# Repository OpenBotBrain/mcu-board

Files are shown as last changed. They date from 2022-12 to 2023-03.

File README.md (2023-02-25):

# mcu-board

Some design notes for an MCU board...
Deeply WIP.

## Features

1. STM32 Cortex M4 with FSMC (possibility: STM32F413ZGT6 for 144-LQFP,
   STM32F413VGT3 for 100-LQFP, and STM32F413RGT6 for 64-LQFP)
2. Extra flash and PSRAM
2. WIFI module e.g. [ESP32 C3](https://www.espressif.com/sites/default/files/documentation/esp32-c3-mini-1_datasheet_en.pdf) or [ESP32 S3](https://www.espressif.com/sites/default/files/documentation/esp32-s3-mini-1_mini-1u_datasheet_en.pdf)
3. 4 motor control ports (EV3 compatible)
4. 4 sensor control ports (EV3 compatible)
5. Raspberry Pi pin-out connector (enough to communicate with
   Raspberry pi Zero, does not need full support)
5. SD card (SPI interface enough/SDIO nice to have but requires supported MCU)
6. Accelerometer (could be external)
7. STEMMA QT connector (nice to have)
8. Some informative display (nice to have)
9. A couple of buttons for interface (nice to have also)
10. Lego "compatible" physical shape.

### Alternative

- STM32L4R5VGT6 with 640KB of RAM instead of the external ram versions
  (but it also supports the FMC/FSMC). And it is cheap, and more
  available than the previous ones. (Or the subtly better STM32L4R5VIT6)

### Notes

- The [WIFI
  module](https://www.digikey.co.uk/en/products/detail/espressif-systems/ESP32-C3-MINI-1-H4/14548892)
  with the SD card on one side and the Raspberry Pi connector may not
  need to be active at the same time.
- The display could be controlled by the WIFI module via [AT
  commands](https://docs.espressif.com/projects/esp-at/en/latest/esp32/Compile_and_Develop/How_to_add_user-defined_AT_commands.html).
  Other things could be moved to the WIFI module too (the interface
  buttons, maybe).
- The board would be a [Raspberry Pi
  hat](https://github.com/raspberrypi/hats) that can work alone. This
  can be a rev 2 objective, but planning for the space would not hurt.
- Driving external memories with the FSMC, application not AN4761

# smaller mcu-board

## Features

1. STM32 Cortex M4 - May be
   - STM32L4P5CGT6
   - STM32L4P5CGT6P
   - STM32L4Q5CGT6
   - STM32L4Q5CGT6P
all (48-LQFP with 1MB of flash, and 320KB of RAM).

2. WIFI module e.g. [ESP32 C3](https://www.espressif.com/sites/default/files/documentation/esp32-c3-mini-1_datasheet_en.pdf) or [ESP32 S3](https://www.espressif.com/sites/default/files/documentation/esp32-s3-mini-1_mini-1u_datasheet_en.pdf)

3. 4 motor control ports (EV3 compatible)
4. 4 sensor control ports (EV3 compatible)

5. Raspberry Pi pin-out connector (enough to communicate with
   Raspberry pi Zero, does not need full support)

5. SD card (SPI interface enough/SDIO nice to have but requires supported MCU)
6. Accelerometer (could be external)
7. STEMMA QT connector (nice to have)
8. Some informative display and a couple of LEDs (nice to have)
9. A couple of buttons for interface (nice to have also)
10. Lego "compatible" physical shape.

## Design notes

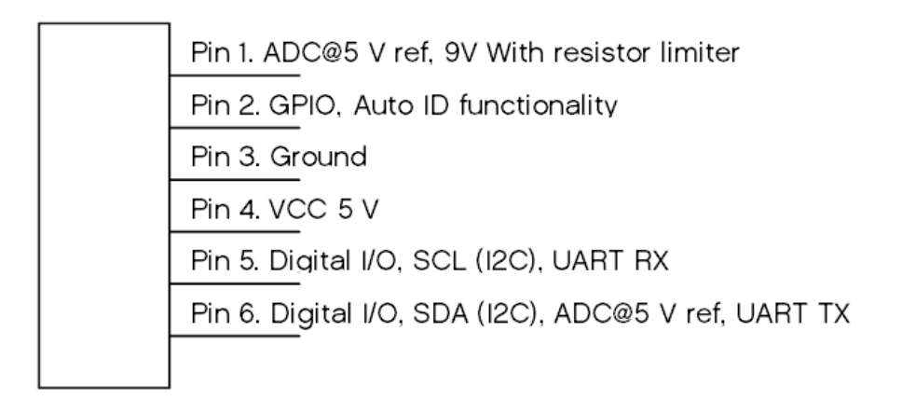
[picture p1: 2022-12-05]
PCB-RevA/input_port_pinout.png

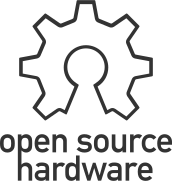
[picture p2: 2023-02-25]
PCB-RevA/OpenSourceHardware.png

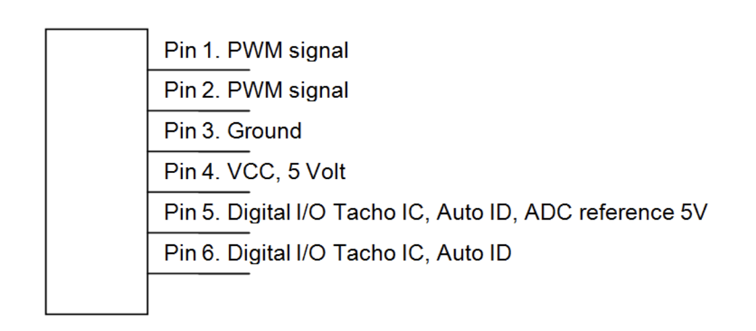
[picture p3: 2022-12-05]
PCB-RevA/ouput_port_pinout.png

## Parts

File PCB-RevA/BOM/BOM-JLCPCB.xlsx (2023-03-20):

Designator | Comment | Footprint | Qty | JLCPCB Part
C1, C4, C5, C6, C7, C8, C10, C12, C14, C18, C20, C23, C24, C25, C26, C27, C28, C29, C30, C31, C32, C38, C39, C41, C42, C45, C46, C52, C54, C55, C58, C62, C63, C68, C71, C72, C76, C93, C113, C141, C142, C143, C144, C145, C146, C166, C167, C168, C169, C170, C171, C180, C182 | 100n | Capacitor_SMD:C_0402_1005Metric | 53 | C1525 | https://www.lcsc.com/product-detail/Multilayer-Ceramic-Capacitors-MLCC-SMD-SMT_Samsung-Electro-Mechanics-CL05B104KO5NNNC_C1525.html
C2, C3, C16, C17, C19, C33, C34, C35, C36, C37, C43, C53, C90, C91, C92, C94, C99, C110, C110, C112, C114, C119, C132, C135, C140, C157, C160, C165, C181 | 1u 16V | Capacitor_SMD:C_0603_1608Metric | 29 | C59302 | https://www.lcsc.com/product-detail/Multilayer-Ceramic-Capacitors-MLCC-SMD-SMT_FH-Guangdong-Fenghua-Advanced-Tech-0603B105K250NT_C59302.html
C9, C49, C50, C51, C56, C73, C74, C75, C77, C78, C79 | 10u | Capacitor_SMD:C_0805_2012Metric | 11 | C1713 | https://www.lcsc.com/product-detail/Multilayer-Ceramic-Capacitors-MLCC-SMD-SMT_Samsung-Electro-Mechanics-CL21A106KOQNNNE_C1713.html
C11, C13, C60, C149, C174 | 4u7 16V | Capacitor_SMD:C_0603_1608Metric | 5 | C19666 | https://www.lcsc.com/product-detail/Multilayer-Ceramic-Capacitors-MLCC-SMD-SMT_Samsung-Electro-Mechanics-CL10A475KO8NNNC_C19666.html
C15, C80, C81, C86, C87, C88, C89, C97, C98, C108, C109, C117, C118, C128, C129, C133, C134, C138, C139, C150, C158, C159, C163, C164, C175 | 10n | Capacitor_SMD:C_0402_1005Metric | 25 | C15195 | https://www.lcsc.com/product-detail/Multilayer-Ceramic-Capacitors-MLCC-SMD-SMT_Samsung-Electro-Mechanics-CL05B103KB5NNNC_C15195.html
C21, C22 | 8p | Capacitor_SMD:C_0402_1005Metric | 2 | C610103 | https://www.lcsc.com/product-detail/Multilayer-Ceramic-Capacitors-MLCC-SMD-SMT_VIIYONG-V8R0D0402C0G500NBT_C610103.html
C40, C44, C57, C59, C61, C64, C65, C67, C70, C147, C172 | 10u 16V | Capacitor_SMD:C_0805_2012Metric | 11 | C1713 | https://www.lcsc.com/product-detail/Multilayer-Ceramic-Capacitors-MLCC-SMD-SMT_Samsung-Electro-Mechanics-CL21A106KOQNNNE_C1713.html
C47, C48, C95, C96, C100, C101, C102, C103, C104, C105, C106, C107, C115, C116, C120, C121, C122, C123, C124, C125, C126, C127, C130, C131, C136, C137, C151, C152, C153, C154, C155, C156, C161, C162, C176, C177, C178, C179 | 330p | Capacitor_SMD:C_0402_1005Metric | 38 | C13533 | https://www.lcsc.com/product-detail/Multilayer-Ceramic-Capacitors-MLCC-SMD-SMT_Samsung-Electro-Mechanics-CL05C331JB5NNNC_C13533.html
C66, C69, C148, C173 | 100uF 16V | Capacitor_SMD:CP_Elec_6.3x5.2 | 4 | C125975 | https://www.lcsc.com/product-detail/Aluminum-Electrolytic-Capacitors-SMD_Nichicon-UWT1V101MCL1GS_C125975.html
C82, C83 | 47p | Capacitor_SMD:C_0402_1005Metric | 2 | C1567 | https://www.lcsc.com/product-detail/Multilayer-Ceramic-Capacitors-MLCC-SMD-SMT_FH-Guangdong-Fenghua-Advanced-Tech-0402CG470J500NT_C1567.html
C84, C85 | 2.2n | Capacitor_SMD:C_0402_1005Metric | 2 | C1531 | https://www.lcsc.com/product-detail/Multilayer-Ceramic-Capacitors-MLCC-SMD-SMT_FH-Guangdong-Fenghua-Advanced-Tech-0402B222K500NT_C1531.html
D1, D2, D3, D3, D8, D9, D10 | LED | LED_SMD:LED_0402_1005Metric | 6 | C434447 | https://www.lcsc.com/product-detail/Light-Emitting-Diodes-LED_Yongyu-Photoelectric-SZYY0402B_C434447.html
D4, D5 | ESD5Zxx | Diode_SMD:D_SOD-523 | 2 | C5369351 | https://www.lcsc.com/product-detail/span-style-background-color-ff0-ESD-span-Protection-Devices_LGE-ESD5Z15_C5369351.html
D6, D7, D17, D18, D21, D22, D25, D26, D31, D32, D35, D36, D39, D40, D41, D42, D45, D46, D53, D54, D57, D58 | ESD9B5.0ST5G | Diode_SMD:D_SOD-923 | 22 | C2835422 | https://www.lcsc.com/product-detail/span-style-background-color-ff0-ESD-span-Protection-Devices_TECH-PUBLIC-ESD9B5VD_C2835422.html
D13, D14, D15, D16, D19, D20, D23, D24, D27, D28, D29, D30, D33, D34, D37, D38, D43, D44, D47, D48, D55, D56, D59, D60 | BAT54S | Package_TO_SOT_SMD:SOT-23 | 24 | C181201 | https://www.lcsc.com/product-detail/Schottky-Barrier-Diodes-SBD_Guangdong-Hottech-BAT54S_C181201.html
D49, D50, D51, D52, D61, D62, D63, D64 | SD12_SOD323 | Diode_SMD:D_SOD-323 | 8 | C521915 | https://www.lcsc.com/product-detail/ESD-Protection-Devices_TECH-PUBLIC-ESD5V0B03-323_C521915.html
F1, F2 | 8V 2A | Resistor_SMD:R_1812_4532Metric | 2 | C883156 | https://www.lcsc.com/product-detail/Resettable-Fuses_BHFUSE-BSMD1812-200-16V_C883156.html
F3, F4, F5, F6, F7, F8, F9, F10 | 30mA | Resistor_SMD:R_0603_1608Metric | 8 | C914090 | https://www.lcsc.com/product-detail/Resettable-Fuses_BHFUSE-BSMD0603-003-30V_C914090.html
J1 | DF11-10DP-2DSA | Connector_JST:JST_PHD_B10B-PHDSS_2x05_P2.00mm_Vertical | 1 | C597822 | https://www.lcsc.com/product-detail/Wire-To-Board-Wire-To-Wire-Connector_HRS-Hirose-DF11-10DP-2DSA-24_C597822.html
J3 | USB_C_Receptacle_USB2.0 | Connector_USB:USB_C_Receptacle_Palconn_UTC16-G | 1 | C2988369 | https://www.lcsc.com/product-detail/USB-Connectors_G-Switch-GT-USB-7010ASV_C2988369.html
L1 | 1.2uH 6.5A | Inductor_SMD:L_Chilisin_BMRA00050520 |  | C2041615 | https://www.lcsc.com/product-detail/Inductors-SMD_Vishay-Intertech-IHLP2020CZER1R5M11_C2041615.html
L2, L3 | 6.8uH 3.6A | Inductor_SMD:L_Ferrocore_DLG-0504 | 2 | C2847478 | https://www.lcsc.com/product-detail/Inductors-SMD_KOHERelec-MDA5030-6R8M_C2847478.html
Q1, Q2, Q3, Q5, Q6, Q9, Q10, Q11, Q12, Q17, Q18 | BSS84 | Package_TO_SOT_SMD:SOT-23 | 11 | C8492 | https://www.lcsc.com/product-detail/MOSFETs_LRC-LBSS84LT1G_C8492.html
Q4, Q7, Q8, Q13, Q15, Q16, Q19, Q20, Q27, Q28, Q29, Q30, Q31, Q32, Q33, Q34, Q35, Q36, Q37 | 2N7002 | Package_TO_SOT_SMD:SOT-23 | 19 | C8545 | https://www.lcsc.com/product-detail/MOSFETs_Jiangsu-Changjing-Electronics-Technology-Co-Ltd-2N7002_C8545.html
R1, R2, R3, R4, R6, R7, R8, R13, R14, R15, R16, R17, R18, R19, R20, R31, R33, R39, R40, R41, R43, R51, R53, R55, R57, R61, R62, R65, R68, R70, R71, R72, R73, R74, R75, R84, R85, R90, R91, R92, R93, R94, R95, R96, R97, R110, R111, R112, R114, R124, R125, R134, R135, R140, R141, R412, R143, R144, R145, R146, R147, R160, R161, R162, R164 | 10K | Resistor_SMD:R_0402_1005Metric | 65 | C25744 | https://www.lcsc.com/product-detail/Chip-Resistor-Surface-Mount_UNI-ROYAL-Uniroyal-Elec-0402WGF1002TCE_C25744.html
R5, R9, R28, R29, R30, R32, R34, R36, R37, R38, R44, R46, R48, R49, R52, R152 | 22 | Resistor_SMD:R_0402_1005Metric | 16 | C25092 | https://www.lcsc.com/product-detail/Chip-Resistor-Surface-Mount_UNI-ROYAL-Uniroyal-Elec-0402WGF220JTCE_C25092.html
R10, R11, R12, R23, R24, R25, R35, R50, R78, R79, R80, R81, R100, R101, R104, R105, R107, R109, R113, R115, R128, R129, R130, R131, R150, R151, R153, R163, R165, R184, R185, R198, R199, R202, R203, R204, R205, R206, R219, R220, R233, R234, R237, R238, R239, R240 | 330 | Resistor_SMD:R_0402_1005Metric | 46 | C25104 | https://www.lcsc.com/product-detail/Chip-Resistor-Surface-Mount_UNI-ROYAL-Uniroyal-Elec-0402WGF3300TCE_C25104.html
R21, R22, R26, R27, R45, R47, R54, R56, R69, R86, R87, R120, R121, R136, R137, R170, R171, R178, R179, R192, R193, R213, R214, R227, R228 | 2K4 | Resistor_SMD:R_0402_1005Metric | 25 | C25882 | https://www.lcsc.com/product-detail/Chip-Resistor-Surface-Mount_UNI-ROYAL-Uniroyal-Elec-0402WGF2401TCE_C25882.html
R42, R116, R118, R166, R168 | 220K | Resistor_SMD:R_0402_1005Metric | 5 | C25767 | https://www.lcsc.com/product-detail/Chip-Resistor-Surface-Mount_UNI-ROYAL-Uniroyal-Elec-0402WGF2203TCE_C25767.html
R58, R76, R77, R82, R83, R98, R99, R102, R103, R106, R108, R117, R119, R126, R127, R132, R133, R148, R149, R154, R167, R169, R174, R175, R180, R181, R186, R187, R188, R189, R194, R195, R200, R201, R209, R210, R215, R216, R221, R222, R223, R224, R229, R230, R235, R236 | 100K | Resistor_SMD:R_0402_1005Metric | 46 | C25741 | https://www.lcsc.com/product-detail/Chip-Resistor-Surface-Mount_UNI-ROYAL-Uniroyal-Elec-0402WGF1003TCE_C25741.html
R59, R67 | 29K4 | Resistor_SMD:R_0402_1005Metric | 2 | C327356 | https://www.lcsc.com/product-detail/Chip-Resistor-Surface-Mount_YAGEO-RC0402FR-0729K4L_C327356.html
R60, R63, R64, R66 | 51K | Resistor_SMD:R_0402_1005Metric | 4 | C25794 | https://www.lcsc.com/product-detail/Chip-Resistor-Surface-Mount_UNI-ROYAL-Uniroyal-Elec-0402WGF5102TCE_C25794.html
R88, R89, R122, R123, R138, R139, R172, R173, R176, R177, R182, R183, R190, R191, R196, R197, R211, R212, R217, R218, R225, R226, R231, R232 | 4K7 | Resistor_SMD:R_0402_1005Metric | 24 | C25900 | https://www.lcsc.com/product-detail/Chip-Resistor-Surface-Mount_UNI-ROYAL-Uniroyal-Elec-0402WGF4701TCE_C25900.html
R207, R208, R242, R243 | 0.43 | Resistor_SMD:R_0805_2012Metric | 4 | C3000778 | https://www.lcsc.com/product-detail/Chip-Resistor-Surface-Mount_FOJAN-FRL0805JR400TS_C3000778.html
SW1, SW2, SW3, SW5 | SW_Omron_B3FS | Button_Switch_SMD:SW_Push_1P1T_NO_6x6mm_H9.5mm | 4 | C255812 | https://www.lcsc.com/product-detail/Tactile-Switches_HYP-Hongyuan-Precision-1TS005F-2500-5001_C255812.html
U1 | LSM6DSL | Package_LGA:LGA-14_3x2.5mm_P0.5mm_LayoutBorder3x4y | 1 | C126672 | https://www.lcsc.com/product-detail/Attitude-Sensor-Gyroscope_STMicroelectronics-LSM6DSLTR_C126672.html
U2 | STM32L496ZGTx | Package_QFP:LQFP-144_20x20mm_P0.5mm | 1 | C1337220 | https://www.lcsc.com/product-detail/Microcontroller-Units-MCUs-MPUs-SOCs_STMicroelectronics-STM32L496ZGT6_C1337220.html
U4 | W25X40CLSS | Package_SO:SOIC-8_5.275x5.275mm_P1.27mm | 1 | C82317 (https://www.lcsc.com/product-detail/NOR-FLASH_Winbond-Elec-W25Q16JVSSIQ_C82317.html) | https://www.lcsc.com/product-detail/NOR-FLASH_Winbond-Elec-W25Q16JVSSIQ_C82317.html
U5 | FUSB302B01MPX | Package_DFN_QFN:WQFN-14-1EP_2.5x2.5mm_P0.5mm_EP1.45x1.45mm | 1 | C132291 | https://www.lcsc.com/product-detail/span-style-background-color-ff0-USB-span-ICs_onsemi-FUSB302BMPX_C132291.html
U6 | BQ25601 | Package_DFN_QFN:Texas_S-PWQFN-N24_EP2.7x2.7mm_ThermalVias | 1 | C468236 | https://www.lcsc.com/product-detail/Battery-Management-ICs_Texas-Instruments-BQ25601RTWR_C468236.html
U7 | AP2127K-3.3 | Package_TO_SOT_SMD:SOT-23-5 | 1 | C156285 | https://www.lcsc.com/product-detail/Linear-Voltage-Regulators-LDO_Diodes-Incorporated-AP2127K-3-3TRG1_C156285.html
U8, U9 | PAM2423AECADJR | Package_SO:SOIC-8-1EP_3.9x4.9mm_P1.27mm_EP2.29x3mm_ThermalVias | 2 | C781891 | https://www.lcsc.com/product-detail/DC-DC-Converters_Diodes-Incorporated-PAM2423AECADJR_C781891.html
U10, U11, U12, U18 | LMV324 | Package_SO:SOIC-14_3.9x8.7mm_P1.27mm | 4 | C362275 | https://www.lcsc.com/product-detail/Operational-Amplifier_Gainsil-LMV324-SR_C362275.html
U13, U14, U15, U16, U19, U20, U21, U22 | SN74LVC1G14DBV | Package_TO_SOT_SMD:SOT-23-5 | 8 | C434069 | https://www.lcsc.com/product-detail/Inverters_UMW-Youtai-Semiconductor-Co-Ltd-SN74LVC1G14DBVR_C434069.html
U17, U23 | DRV8833PWP | Package_SO:HTSSOP-16-1EP_4.4x5mm_P0.65mm_EP3.4x5mm_Mask2.46x2.31mm_ThermalVias | 2 | C50506 | https://www.lcsc.com/product-detail/Motor-Driver-ICs_Texas-Instruments-DRV8833PWPR_C50506.html
Y2 | 8Z-24.000MAAJ-T | Crystal:Crystal_SMD_Abracon_ABM10-4Pin_2.5x2.0mm | 1 | C284163 | https://www.lcsc.com/product-detail/Crystals_TAE-Zhejiang-Abel-Elec-TXM24M0004252BBCEO00T_C284163.html

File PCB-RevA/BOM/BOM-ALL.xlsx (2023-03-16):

Reference | Value | Footprint | Datasheet | Digi | Digikey | Field4 | Field5 | digi | Qty
C1, C4-C8, C10, C12, C14, C18, C20, C23-C32, C38, C39, C41, C42, C45, C46, C52, C54, C55, C58, C62, C63, C68, C71, C72, C76, C93, C113, C141-C146, C166-C171, C180, C182 | 100n | Capacitor_SMD:C_0402_1005Metric | https://www.digikey.co.uk/en/products/detail/samsung-electro-mechanics/CL05A104KA5NNNC/3886701 |  |  |  |  | https://www.digikey.co.uk/en/products/detail/samsung-electro-mechanics/CL05A104KA5NNNC/3886701 | 53 | https://www.lcsc.com/product-detail/Multilayer-Ceramic-Capacitors-MLCC-SMD-SMT_Samsung-Electro-Mechanics-CL05B104KO5NNNC_C1525.html
C2, C3, C16, C17, C19, C33-C37, C43, C53, C90-C92, C94, C99, C110-C112, C114, C119, C132, C135, C140, C157, C160, C165, C181 | 1u 16V | Capacitor_SMD:C_0603_1608Metric | https://www.digikey.co.uk/en/products/detail/samsung-electro-mechanics/CL10A105KA8NNNC/3886760 |  |  |  |  | https://www.digikey.co.uk/en/products/detail/samsung-electro-mechanics/CL10A105KA8NNNC/3886760 | 29 | https://www.lcsc.com/product-detail/Multilayer-Ceramic-Capacitors-MLCC-SMD-SMT_FH-Guangdong-Fenghua-Advanced-Tech-0603B105K250NT_C59302.html
C9, C49-C51, C56, C73-C75, C77-C79 | 10u | Capacitor_SMD:C_0805_2012Metric | https://www.digikey.co.uk/en/products/detail/samsung-electro-mechanics/CL21A106KOQNNNE/3886754 | https://www.digikey.co.uk/en/products/detail/samsung-electro-mechanics/CL21A106KOQNNNE/3886754 |  |  |  |  | 11 | https://www.lcsc.com/product-detail/Multilayer-Ceramic-Capacitors-MLCC-SMD-SMT_Samsung-Electro-Mechanics-CL21A106KOQNNNE_C1713.html
C11, C13, C60, C149, C174 | 4u7 16V | Capacitor_SMD:C_0603_1608Metric | https://www.digikey.co.uk/en/products/detail/samsung-electro-mechanics/CL10A105KA8NNNC/3886760 |  |  |  |  | https://www.digikey.co.uk/en/products/detail/samsung-electro-mechanics/CL10A105KA8NNNC/3886760 | 5 | https://www.lcsc.com/product-detail/Multilayer-Ceramic-Capacitors-MLCC-SMD-SMT_Samsung-Electro-Mechanics-CL10A475KO8NNNC_C19666.html
C15, C80, C81, C86-C89, C97, C98, C108, C109, C117, C118, C128, C129, C133, C134, C138, C139, C150, C158, C159, C163, C164, C175 | 10n | Capacitor_SMD:C_0402_1005Metric |  |  |  |  |  |  | 25 | https://www.lcsc.com/product-detail/Multilayer-Ceramic-Capacitors-MLCC-SMD-SMT_YAGEO-CC0402KRX7R9BB103_C60133.html
C21, C22 | 6p8 | Capacitor_SMD:C_0402_1005Metric |  |  |  |  |  |  | 2 | https://www.lcsc.com/product-detail/Multilayer-Ceramic-Capacitors-MLCC-SMD-SMT_FH-Guangdong-Fenghua-Advanced-Tech-0402CG6R8C500NT_C1576.html
C40, C44, C57, C59, C61, C64, C65, C67, C70, C147, C172 | 10u 16V | Capacitor_SMD:C_0805_2012Metric | https://www.digikey.co.uk/en/products/detail/samsung-electro-mechanics/CL21A106KOQNNNE/3886754 | https://www.digikey.co.uk/en/products/detail/samsung-electro-mechanics/CL21A106KOQNNNE/3886754 |  |  |  |  | 11 | https://www.lcsc.com/product-detail/Multilayer-Ceramic-Capacitors-MLCC-SMD-SMT_Samsung-Electro-Mechanics-CL21A106KOQNNNE_C1713.html
C47, C48, C95, C96, C100-C107, C115, C116, C120-C127, C130, C131, C136, C137, C151-C156, C161, C162, C176-C179 | 330p | Capacitor_SMD:C_0402_1005Metric |  |  |  |  |  |  | 38 | https://www.lcsc.com/product-detail/Multilayer-Ceramic-Capacitors-MLCC-SMD-SMT_YAGEO-CC0402KRX7R9BB331_C106206.html
C66, C69, C148, C173 | 100uF 16V | Capacitor_SMD:CP_Elec_6.3x5.2 | ~ |  |  |  |  |  | 4 | https://www.lcsc.com/product-detail/Aluminum-Electrolytic-Capacitors-SMD_Nichicon-UWT1V101MCL1GS_C125975.html
C82, C83 | 47p | Capacitor_SMD:C_0402_1005Metric |  |  |  |  |  |  | 2 | https://www.lcsc.com/product-detail/Multilayer-Ceramic-Capacitors-MLCC-SMD-SMT_YAGEO-CC0402JRNPO9BN470_C60137.html
C84, C85 | 2.2n | Capacitor_SMD:C_0402_1005Metric |  |  |  |  |  |  | 2 | https://www.lcsc.com/product-detail/Multilayer-Ceramic-Capacitors-MLCC-SMD-SMT_YAGEO-CC0402KRX7R9BB222_C106861.html
D1-D3, D8-D10 | LED | LED_SMD:LED_0402_1005Metric | ~ |  |  |  |  |  | 6 | https://www.lcsc.com/product-detail/Light-Emitting-Diodes-LED_Yongyu-Photoelectric-SZYY0402B_C434447.html
D4, D5 | ESD5Zxx | Diode_SMD:D_SOD-523 | https://www.onsemi.com/pdf/datasheet/esd5z2.5t1-d.pdf |  |  | https://www.digikey.co.uk/en/products/detail/littelfuse-inc/AQ3530-01LTG/11503998 |  |  | 2 | https://www.lcsc.com/product-detail/span-style-background-color-ff0-ESD-span-Protection-Devices_LGE-ESD5Z15_C5369351.html
D6, D7, D17, D18, D21, D22, D25, D26, D31, D32, D35, D36, D39-D42, D45, D46, D53, D54, D57, D58 | ESD9B5.0ST5G | Diode_SMD:D_SOD-923 | https://www.onsemi.com/pub/Collateral/ESD9B-D.PDF |  |  |  |  |  | 22 | https://www.lcsc.com/product-detail/span-style-background-color-ff0-ESD-span-Protection-Devices_TECH-PUBLIC-ESD9B5VD_C2835422.html
D11, D12 | FSV330AF | Diode_SMD:D_SOD-128 | ~ |  |  |  |  |  | 2 | https://www.lcsc.com/product-detail/Schottky-Barrier-Diodes-SBD_Comchip-ACDBC560-HF_C3019749.html
D13-D16, D19, D20, D23, D24, D27-D30, D33, D34, D37, D38, D43, D44, D47, D48, D55, D56, D59, D60 | BAT54S | Package_TO_SOT_SMD:SOT-23 | https://www.diodes.com/assets/Datasheets/ds11005.pdf |  |  |  |  |  | 24 | https://www.lcsc.com/product-detail/Schottky-Barrier-Diodes-SBD_Guangdong-Hottech-BAT54S_C181201.html
D49-D52, D61-D64 | SD12_SOD323 | Diode_SMD:D_SOD-323 | https://www.littelfuse.com/~/media/electronics/datasheets/tvs_diode_arrays/littelfuse_tvs_diode_array_sd_c_datasheet.pdf.pdf |  |  |  |  |  | 8
D65 | Inolux_IN-PI554FCH | LED_SMD:LED_Inolux_IN-PI554FCH_PLCC4_5.0x5.0mm_P3.2mm | http://www.inolux-corp.com/datasheet/SMDLED/Addressable%20LED/IN-PI554FCH.pdf |  |  |  |  |  | 1 | https://www.lcsc.com/product-detail/Light-Emitting-Diodes-LED_TCWIN-TX1813M5_C5137307.html
F1, F2 | 8V 2A | Resistor_SMD:R_1812_4532Metric | https://www.digikey.co.uk/en/products/detail/bel-fuse-inc/0ZCG0200FF2C/4156113 |  |  |  |  |  | 2 | https://www.lcsc.com/product-detail/Resettable-Fuses_BHFUSE-BSMD1812-200-16V_C883156.html
F3-F10 | 30mA | Resistor_SMD:R_0603_1608Metric | https://www.digikey.co.uk/en/products/detail/bel-fuse-inc/0ZCM0003FF2G/10270531 |  |  |  |  |  | 8 | https://www.lcsc.com/product-detail/Resettable-Fuses_BHFUSE-BSMD0603-003-30V_C914090.html
FID1-FID4 | Fiducial | Fiducial:Fiducial_1mm_Mask3mm | ~ |  |  |  |  |  | 4
H1-H4 | 3mm | MountingHole:MountingHole_3.2mm_M3_Pad | ~ |  |  |  |  |  | 4
J1 | DF11-10DP-2DSA | Connector_JST:JST_PHD_B10B-PHDSS_2x05_P2.00mm_Vertical | ~ |  |  |  |  |  | 1 | https://www.lcsc.com/product-detail/Wire-To-Board-Wire-To-Wire-Connector_HRS-Hirose-DF11-10DP-2DSA-24_C597822.html
J2 | Raspberry_Pi_2_3 | Connector_PinHeader_2.54mm:PinHeader_2x20_P2.54mm_Vertical | https://www.raspberrypi.org/documentation/hardware/raspberrypi/schematics/rpi_SCH_3bplus_1p0_reduced.pdf |  |  |  |  |  | 1
J3 | USB_C_Receptacle_USB2.0 | Connector_USB:USB_C_Receptacle_Palconn_UTC16-G | https://www.usb.org/sites/default/files/documents/usb_type-c.zip |  |  |  |  |  | 1 | https://www.lcsc.com/product-detail/USB-Connectors_G-Switch-GT-USB-7010ASV_C2988369.html
J4 | Conn_01x02 | Connector_JST:JST_PH_B2B-PH-K_1x02_P2.00mm_Vertical | https://www.digikey.co.uk/en/products/detail/jst-sales-america-inc/B02B-PASK-1-LF-SN/926738 |  |  |  |  |  | 1
J7-J14 | RJ12 | Connector_RJ:RJ12_Amphenol_54601 | https://www.digikey.co.uk/en/products/detail/assmann-wsw-components/A-2004-1-4-LP-N-R/2183634 |  |  |  |  |  | 8 | n/a
L1 | 1.2uH 6.5A | Inductor_SMD:L_Chilisin_BMRA00050520 | https://www.digikey.co.uk/en/products/detail/susumu/PCMB053T-1R2MS/3672031 |  |  |  |  |  | 1 | n/a
L2, L3 | 6.8uH 3.6A | Inductor_SMD:L_Ferrocore_DLG-0504 | https://www.digikey.co.uk/en/products/detail/tdk-corporation/VLS6045EX-6R8M/5287380 |  |  | VLS6045EX-6R8M |  |  | 2 | https://www.lcsc.com/product-detail/Inductors-SMD_KOHERelec-MDA5030-6R8M_C2847478.html
Q1-Q3, Q5, Q6, Q9-Q12, Q17, Q18 | BSS84 | Package_TO_SOT_SMD:SOT-23 | http://assets.nexperia.com/documents/data-sheet/BSS84.pdf |  |  |  |  |  | 11 | https://www.lcsc.com/product-detail/MOSFETs_FOSAN-BSS84_C2926187.html
Q4, Q7, Q8, Q13, Q15, Q16, Q19, Q20, Q27-Q37 | 2N7002 | Package_TO_SOT_SMD:SOT-23 | https://www.onsemi.com/pub/Collateral/NDS7002A-D.PDF |  |  |  |  |  | 19 | https://www.lcsc.com/product-detail/MOSFETs_JSMSEMI-2N7002_C916396.html
R1-R4, R6-R8, R13-R20, R31, R33, R39-R41, R43, R51, R53, R55, R57, R61, R62, R65, R68, R70-R75, R84, R85, R90-R97, R110-R112, R114, R124, R125, R134, R135, R140-R147, R160-R162, R164 | 10K | Resistor_SMD:R_0402_1005Metric | ~ |  |  |  |  |  | 65 | https://www.lcsc.com/product-detail/Chip-Resistor-Surface-Mount_YAGEO-RC0402FR-0710KL_C60490.html
R5, R9, R28-R30, R32, R34, R36-R38, R44, R46, R48, R49, R52, R152 | 22 | Resistor_SMD:R_0402_1005Metric | ~ |  |  |  |  |  | 16 | https://www.lcsc.com/product-detail/Chip-Resistor-Surface-Mount_UNI-ROYAL-Uniroyal-Elec-0402WGJ0220TCE_C25152.html
R10-R12, R23-R25, R35, R50, R78-R81, R100, R101, R104, R105, R107, R109, R113, R115, R128-R131, R150, R151, R153, R163, R165, R184, R185, R198, R199, R202-R206, R219, R220, R233, R234, R237-R240 | 330 | Resistor_SMD:R_0402_1005Metric | ~ |  |  |  |  |  | 46 | https://www.lcsc.com/product-detail/Chip-Resistor-Surface-Mount_UNI-ROYAL-Uniroyal-Elec-0402WGJ0331TCE_C12246.html
R21, R22, R26, R27, R45, R47, R54, R56, R69, R86, R87, R120, R121, R136, R137, R170, R171, R178, R179, R192, R193, R213, R214, R227, R228 | 2K4 | Resistor_SMD:R_0402_1005Metric | ~ |  |  |  |  |  | 25 | https://www.lcsc.com/product-detail/Chip-Resistor-Surface-Mount_YAGEO-RC0402FR-072K4L_C112296.html
R42, R116, R118, R166, R168 | 220K | Resistor_SMD:R_0402_1005Metric | ~ |  |  |  |  |  | 5 | https://www.lcsc.com/product-detail/Chip-Resistor-Surface-Mount_UNI-ROYAL-Uniroyal-Elec-0402WGF2203TCE_C25767.html
R58, R76, R77, R82, R83, R98, R99, R102, R103, R106, R108, R117, R119, R126, R127, R132, R133, R148, R149, R154, R167, R169, R174, R175, R180, R181, R186-R189, R194, R195, R200, R201, R209, R210, R215, R216, R221-R224, R229, R230, R235, R236 | 100K | Resistor_SMD:R_0402_1005Metric | ~ |  |  |  |  |  | 46 | https://www.lcsc.com/product-detail/Chip-Resistor-Surface-Mount_YAGEO-RC0402FR-07100KL_C60491.html
R59, R67 | 29K4 | Resistor_SMD:R_0402_1005Metric | ~ | https://www.digikey.co.uk/en/products/detail/stackpole-electronics-inc/RMCF0402FT29K4/1761483 |  |  |  |  | 2 | https://www.lcsc.com/product-detail/Chip-Resistor-Surface-Mount_YAGEO-RC0402FR-0729K4L_C327356.html
R60, R63, R64, R66 | 51K | Resistor_SMD:R_0402_1005Metric | ~ | https://www.digikey.co.uk/en/products/detail/stackpole-electronics-inc/RMCF0402FT29K4/1761483 |  |  |  |  | 4 | https://www.lcsc.com/product-detail/Chip-Resistor-Surface-Mount_UNI-ROYAL-Uniroyal-Elec-0402WGF5102TCE_C25794.html
R88, R89, R122, R123, R138, R139, R172, R173, R176, R177, R182, R183, R190, R191, R196, R197, R211, R212, R217, R218, R225, R226, R231, R232 | 4K7 | Resistor_SMD:R_0402_1005Metric | ~ |  |  |  |  |  | 24 | https://www.lcsc.com/product-detail/Chip-Resistor-Surface-Mount_YAGEO-RC0402FR-074K7L_C105871.html
R207, R208, R242, R243 | 0.43 | Resistor_SMD:R_0805_2012Metric | https://www.digikey.co.uk/en/products/detail/panasonic-electronic-components/ERJ-6DQFR43V/6004382 |  |  |  |  |  | 4 | https://www.lcsc.com/product-detail/Chip-Resistor-Surface-Mount_FOJAN-FRL0805JR430TS_C2930326.html
SW1-SW3, SW5 | SW_Omron_B3FS | Button_Switch_SMD:SW_Push_1P1T_NO_6x6mm_H9.5mm | https://omronfs.omron.com/en_US/ecb/products/pdf/en-b3fs.pdf |  |  |  |  |  | 4 | n/a?
SYMBOL1 |  | CustomLibrary:sggtav_logo |  |  |  |  |  |  | 1
SYMBOL2 |  | CustomLibrary:lego_robot_controller |  |  |  |  |  |  | 1
SYMBOL3 |  | CustomLibrary:open_source |  |  |  |  |  |  | 1
TP1-TP14, TP16, TP18, TP20, TP22, TP24-TP27, TP29-TP101, TP103-TP120, TP122-TP132, TP134-TP145, TP148 | S1mm | TestPoint:TestPoint_Pad_1.0x1.0mm | ~ |  |  |  |  |  | 137
TP15, TP17, TP19, TP21, TP23, TP28, TP133, TP146, TP147, TP149 | TH1mm | TestPoint:TestPoint_THTPad_1.0x1.0mm_Drill0.5mm | ~ |  |  |  |  |  | 10
U1 | LSM6DSL | Package_LGA:LGA-14_3x2.5mm_P0.5mm_LayoutBorder3x4y | https://www.st.com/resource/en/datasheet/lsm6dsl.pdf |  |  |  |  |  | 1 | https://www.lcsc.com/product-detail/Attitude-Sensor-Gyroscope_STMicroelectronics-LSM6DSLTR_C126672.html
U2 | STM32L496ZGTx | Package_QFP:LQFP-144_20x20mm_P0.5mm | https://www.st.com/resource/en/datasheet/stm32l496zg.pdf |  |  |  |  |  | 1 | https://www.lcsc.com/product-detail/Microcontroller-Units-MCUs-MPUs-SOCs_STMicroelectronics-STM32L496ZGT6_C1337220.html
U3 | SSD1306 | SSD1306:128x64OLED |  |  |  |  |  |  | 1
U4 | W25X40CLSS | Package_SO:SOIC-8_5.275x5.275mm_P1.27mm | https://www.winbond.com/resource-files/W25X40CL_G%2020210505.pdf |  |  |  |  |  | 1 | https://www.lcsc.com/product-detail/NOR-FLASH_Winbond-Elec-W25Q16JVSNIQ_C115407.html
U5 | FUSB302B01MPX | Package_DFN_QFN:WQFN-14-1EP_2.5x2.5mm_P0.5mm_EP1.45x1.45mm | http://www.onsemi.com/pub/Collateral/FUSB302B-D.PDF |  |  |  |  |  | 1 | https://www.lcsc.com/product-detail/span-style-background-color-ff0-USB-span-ICs_onsemi-FUSB302BMPX_C132291.html
U6 | BQ25601 | Package_DFN_QFN:Texas_S-PWQFN-N24_EP2.7x2.7mm_ThermalVias | http://www.ti.com/lit/ds/symlink/bq25601.pdf |  |  |  |  |  | 1 | https://www.lcsc.com/product-detail/Battery-Management-ICs_Texas-Instruments-BQ25601RTWR_C468236.html
U7 | AP2127K-3.3 | Package_TO_SOT_SMD:SOT-23-5 | https://www.diodes.com/assets/Datasheets/AP2127.pdf |  |  |  |  |  | 1 | https://www.lcsc.com/product-detail/Linear-Voltage-Regulators-LDO_Diodes-Incorporated-AP2127K-3-3TRG1_C156285.html
U8, U9 | PAM2423AECADJR | Package_SO:SOIC-8-1EP_3.9x4.9mm_P1.27mm_EP2.29x3mm_ThermalVias | https://www.diodes.com/assets/Datasheets/products_inactive_data/PAM2421_22_23.pdf |  | https://www.digikey.co.uk/en/products/detail/diodes-incorporated/PAM2423AECADJR/4033258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 |  |  |  | 2 | https://www.lcsc.com/product-detail/DC-DC-Converters_Diodes-Incorporated-PAM2423AECADJR_C781891.html
U10-U12, U18 | LMV324 | Package_SO:SOIC-14_3.9x8.7mm_P1.27mm | http://www.ti.com/lit/ds/symlink/lmv324.pdf |  |  |  |  |  | 4 | https://www.lcsc.com/product-detail/Operational-Amplifier_TECH-PUBLIC-LMV324_C5342379.html
U13-U16, U19-U22 | SN74LVC1G14DBV | Package_TO_SOT_SMD:SOT-23-5 | http://www.ti.com/lit/ds/symlink/sn74lvc1g14.pdf |  |  |  |  |  | 8 | https://www.lcsc.com/product-detail/Gates_UMW-Youtai-Semiconductor-Co-Ltd-SN74LVC1G14DCKR_C2976657.html
U17, U23 | DRV8833PWP | Package_SO:HTSSOP-16-1EP_4.4x5mm_P0.65mm_EP3.4x5mm_Mask2.46x2.31mm_ThermalVias | http://www.ti.com/lit/ds/symlink/drv8833.pdf |  |  |  |  |  | 2 | https://www.lcsc.com/product-detail/Motor-Driver-ICs_Texas-Instruments-DRV8833PWPR_C50506.html
Y2 | 8Z-24.000MAAJ-T | Crystal:Crystal_SMD_Abracon_ABM10-4Pin_2.5x2.0mm | ~ |  |  |  |  |  | 1 | https://datasheet.lcsc.com/lcsc/1810171034_TAE-Zhejiang-Abel-Elec-TXM24M0004252BBCEO00T_C284163.pdf

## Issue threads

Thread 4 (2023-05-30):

Add a SW to turn on 5V reg and 9V power supply

sggtav, 2023-05-30:
This is to avoid high current spikes when capacitors are getting charged.

sggtav, 2023-10-28:
For testing, we connected a P most in the 4.2 input rail, and the gate is controlled by the uC. This works perfecly

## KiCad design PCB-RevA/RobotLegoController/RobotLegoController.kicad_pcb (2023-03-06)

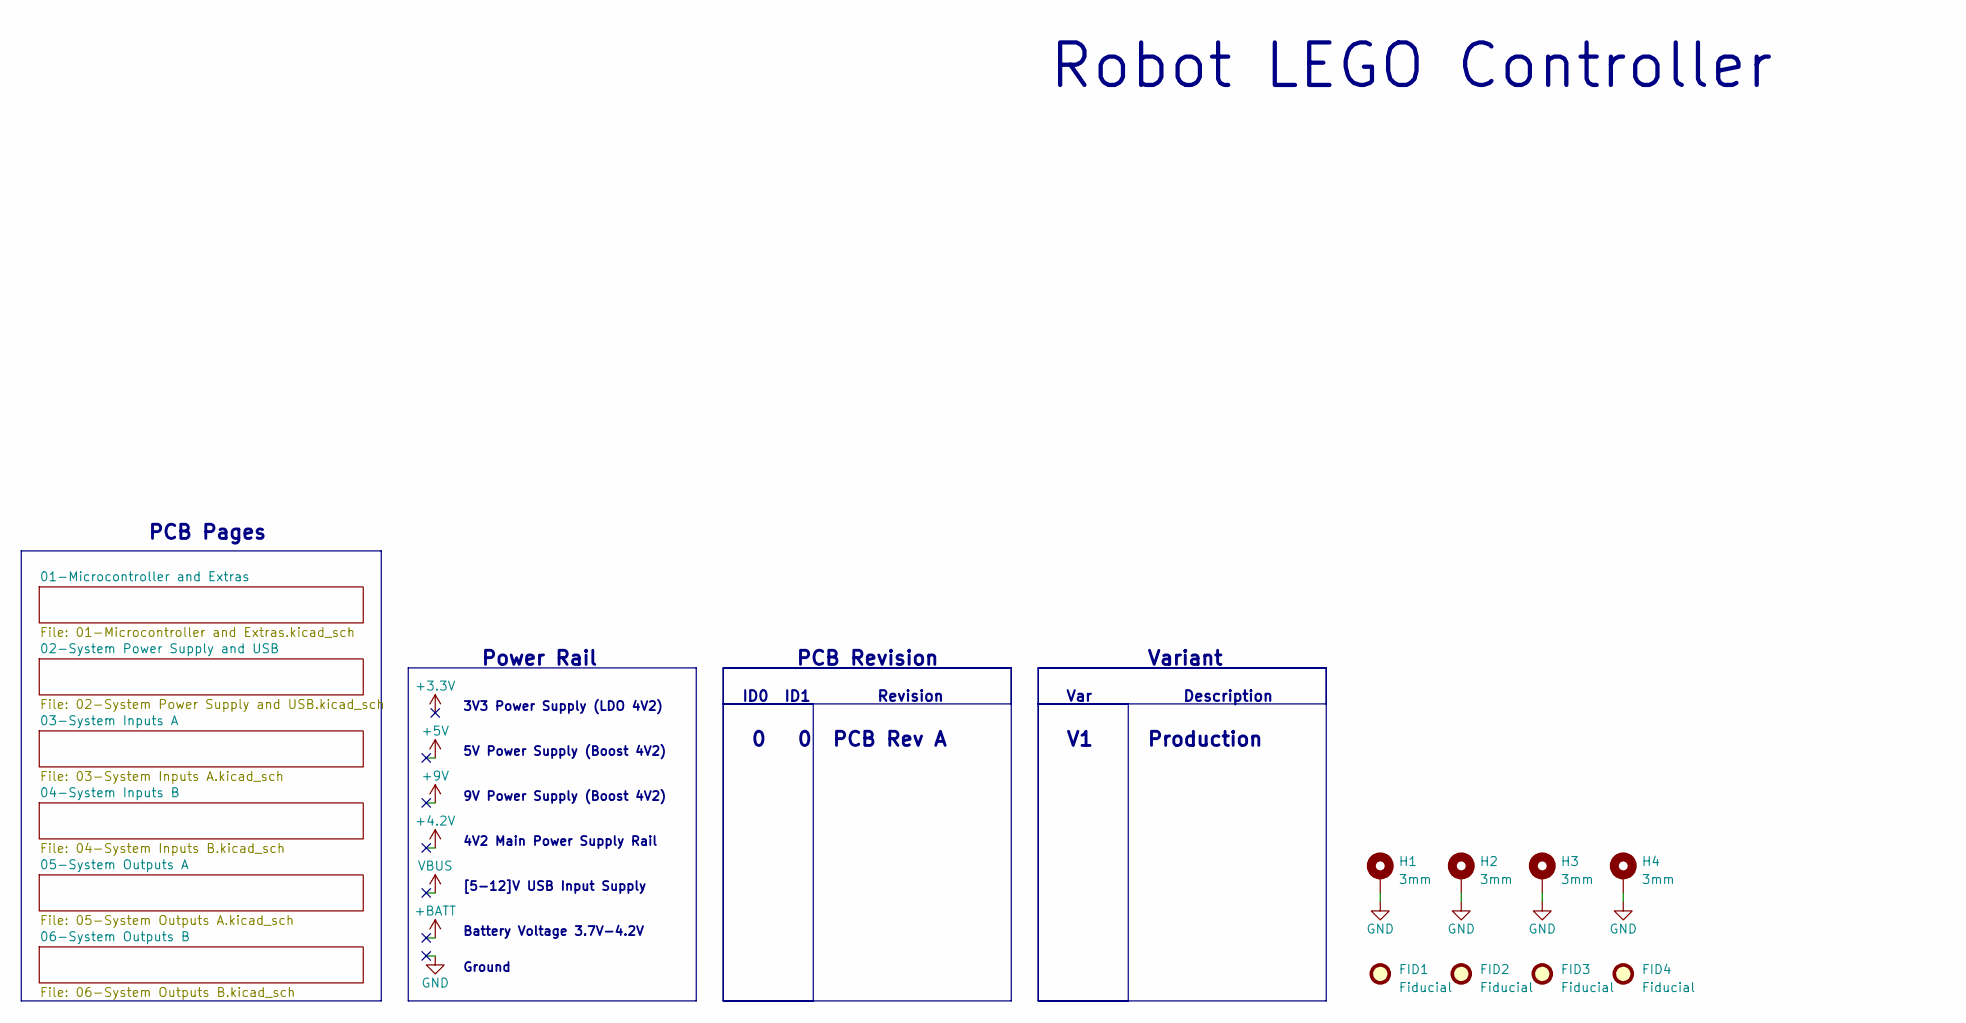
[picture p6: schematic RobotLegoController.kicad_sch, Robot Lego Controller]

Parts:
FID1, FID2, FID3, FID4: Fiducial; Fiducial_1mm_Mask3mm
H1, H2, H3, H4: 3mm; MountingHole_3.2mm_M3_Pad

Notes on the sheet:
Power Rail
Var
0 0
ID0 ID1
9V Power Supply (Boost 4V2)
3V3 Power Supply (LDO 4V2)
Battery Voltage 3.7V-4.2V
Variant
[5-12]V USB Input Supply
Description
Production
PCB Revision
PCB Rev A
4V2 Main Power Supply Rail
Revision
PCB Pages
Ground
5V Power Supply (Boost 4V2)
Robot LEGO Controller

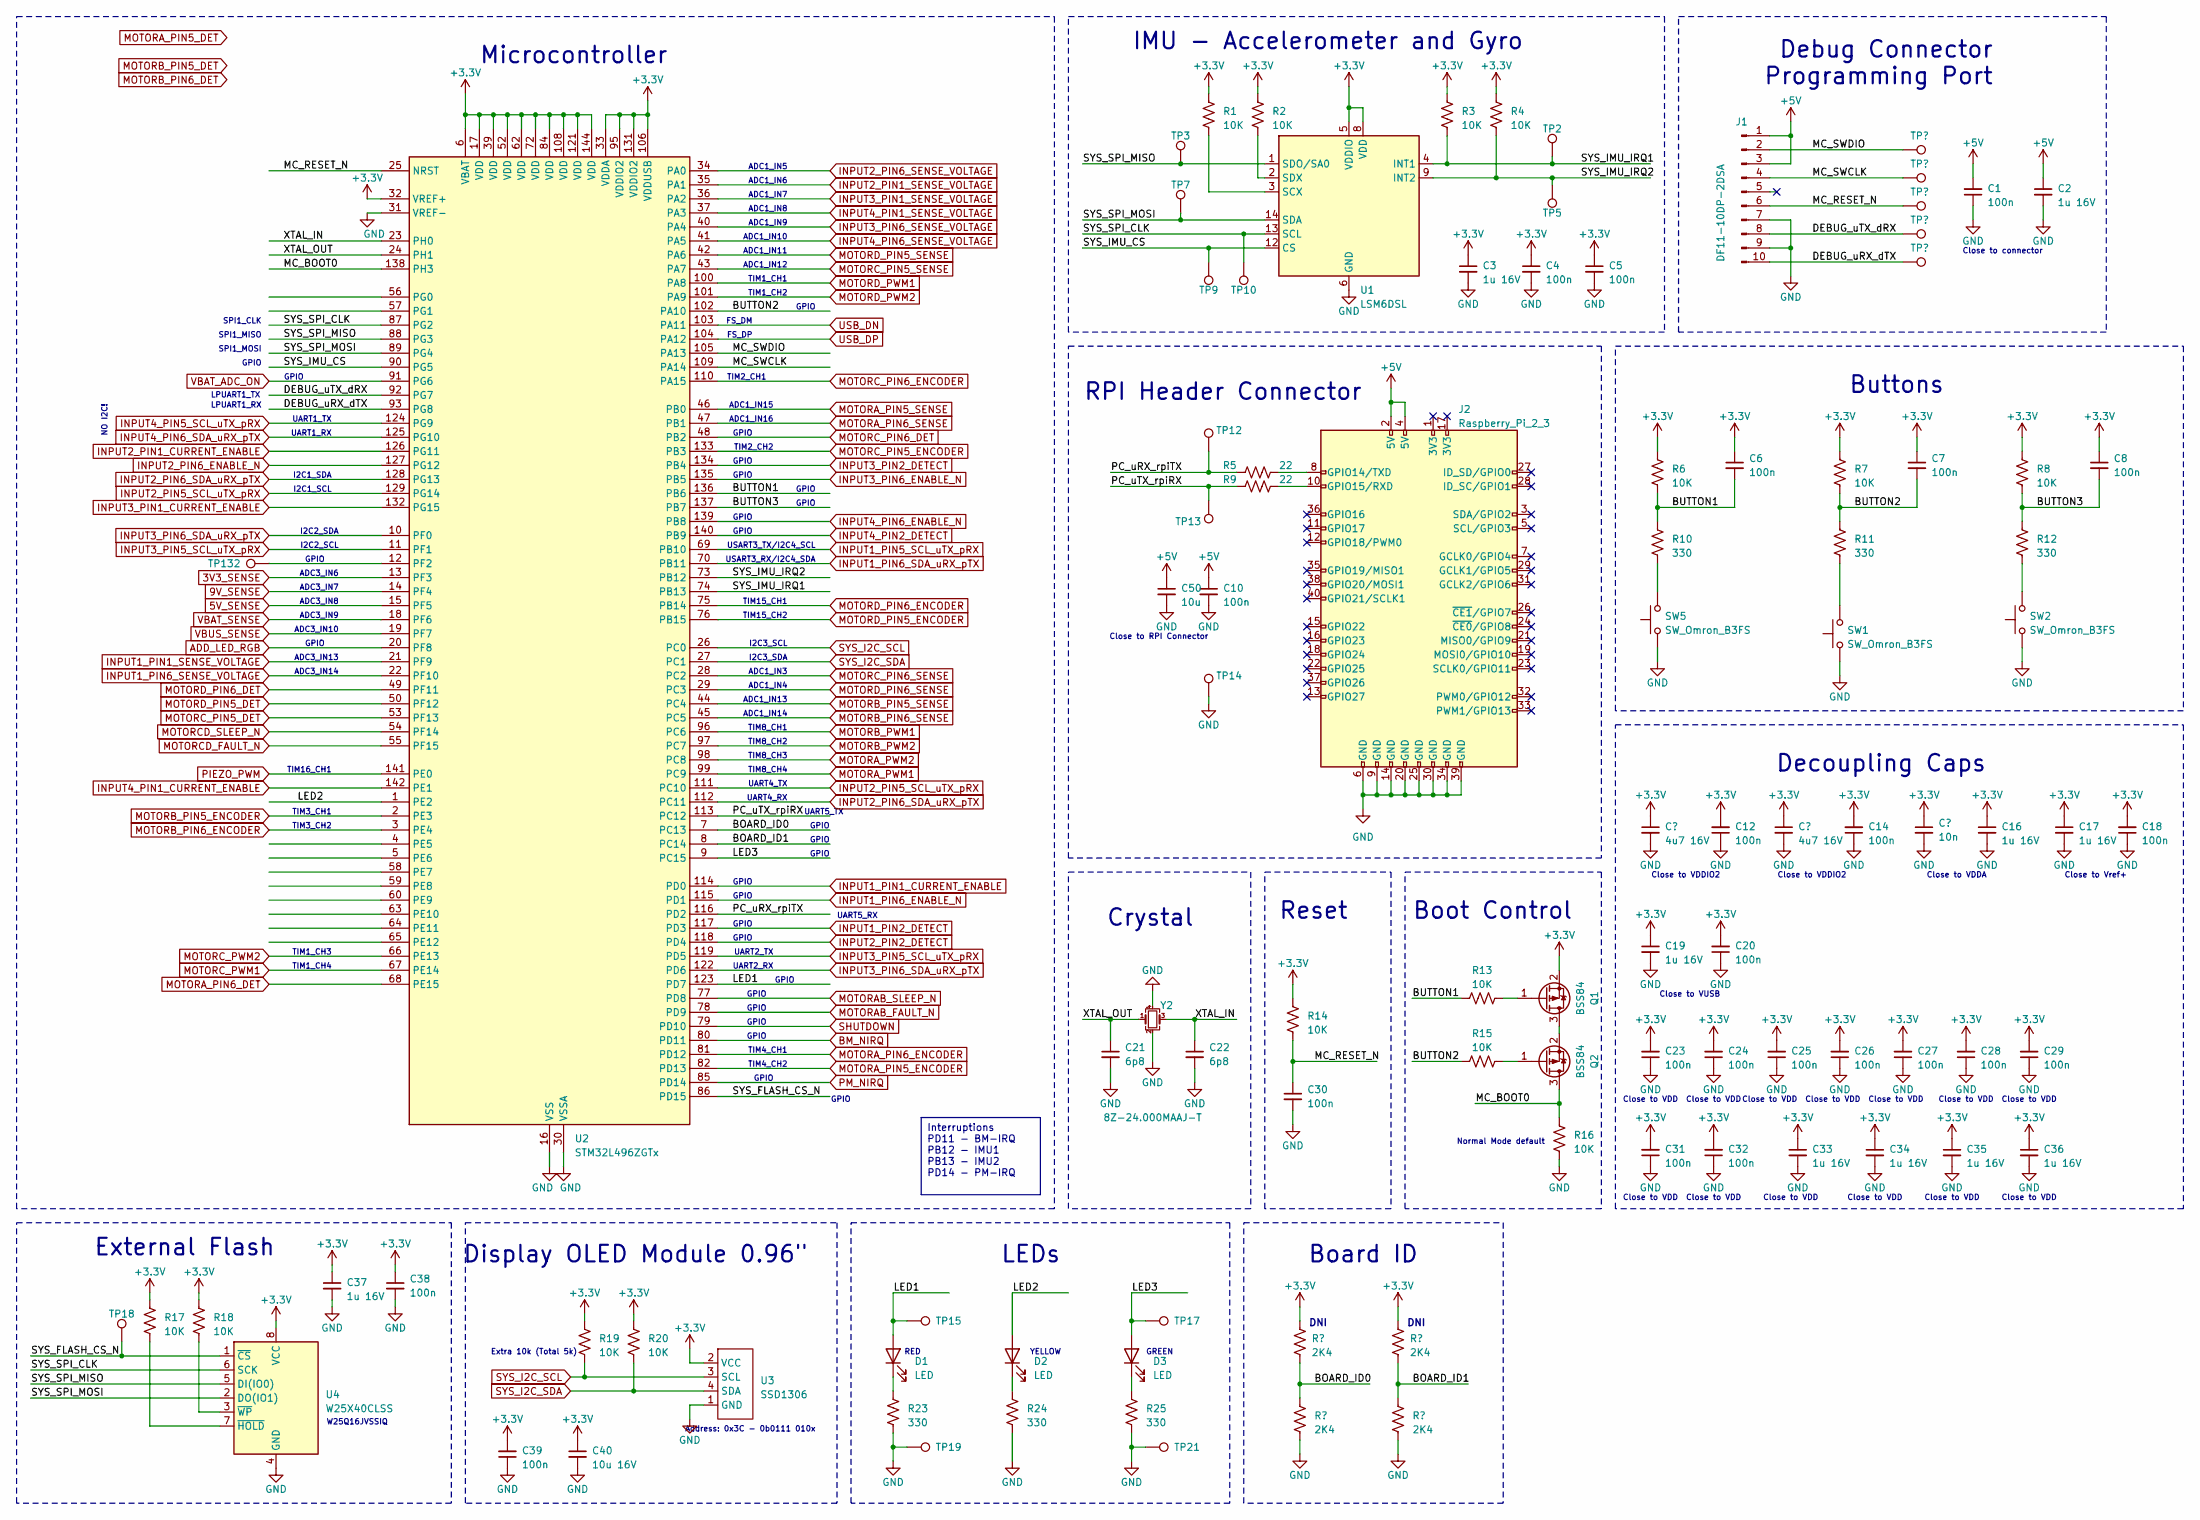
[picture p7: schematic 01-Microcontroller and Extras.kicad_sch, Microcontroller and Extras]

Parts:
C1, C4, C5, C6, C7, C8, C10, C12, C14, C18, C20, C23, C24, C25, C26, C27, C28, C29, C30, C31, C32, C38, C39: 100n; C_0402_1005Metric
C2, C3, C16, C17, C19, C33, C34, C35, C36, C37: 1u 16V; C_0603_1608Metric
C11, C13: 4u7 16V; C_0603_1608Metric
C15: 10n; C_0402_1005Metric
C21, C22: 6p8; C_0402_1005Metric
C40: 10u 16V; C_0805_2012Metric
C50: 10u; C_0805_2012Metric
D1, D2, D3: LED; LED_0402_1005Metric
J1: DF11-10DP-2DSA; JST_PHD_B10B-PHDSS_2x05_P2.00mm_Vertical
J2: Raspberry_Pi_2_3; PinHeader_2x20_P2.54mm_Vertical
Q1, Q2: BSS84; SOT-23
R1, R2, R3, R4, R6, R7, R8, R13, R14, R15, R16, R17, R18, R19, R20: 10K; R_0402_1005Metric
R5, R9: 22; R_0402_1005Metric
R10, R11, R12, R23, R24, R25: 330; R_0402_1005Metric
R21, R22, R26, R27: 2K4; R_0402_1005Metric
SW1, SW2, SW5: SW_Omron_B3FS; SW_Push_1P1T_NO_6x6mm_H9.5mm
TP1, TP2, TP3, TP4, TP5, TP6, TP7, TP8, TP9, TP10, TP11, TP12, TP13, TP14, TP18, TP132: S1mm; TestPoint_Pad_1.0x1.0mm
TP15, TP17, TP19, TP21: TH1mm; TestPoint_THTPad_1.0x1.0mm_Drill0.5mm
U1: LSM6DSL; LGA-14_3x2.5mm_P0.5mm_LayoutBorder3x4y
U2: STM32L496ZGTx; LQFP-144_20x20mm_P0.5mm
U3: SSD1306; 128x64OLED
U4: W25X40CLSS; SOIC-8_5.275x5.275mm_P1.27mm
Y2: 8Z-24.000MAAJ-T; Crystal_SMD_Abracon_ABM10-4Pin_2.5x2.0mm

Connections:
3V3_SENSE: U2.13 (PF3); also elsewhere on the board
5V_SENSE: U2.15 (PF5); also elsewhere on the board
9V_SENSE: U2.14 (PF4); also elsewhere on the board
+3.3V: C3.1, C4.1, C5.1, C6.1, C7.1, C8.1, C11.1, C12.2, C13.1, C14.2, C15.1, C16.1, C17.1, C18.2, C19.1, C20.2, C23.2, C24.2, C25.2, C26.2, C27.2, C28.2, C29.2, C31.2, C32.2, C33.1, C34.1, C35.1, C36.1, C37.1, C38.1, C39.2, C40.1, Q1.2 (S), R1.2, R2.2, R3.2, R4.2, R6.2, R7.2, R8.2, R14.2, R17.2, R18.2, R19.2, R20.2, R21.2, R22.2, U1.5 (VDDIO), U1.8 (VDD), U2.6 (VBAT), U2.17 (VDD), U2.32 (VREF+), U2.33 (VDDA), U2.39 (VDD), U2.52 (VDD), U2.62 (VDD), U2.72 (VDD), U2.84 (VDD), U2.95 (VDDIO2), U2.106 (VDDUSB), U2.108 (VDD), U2.121 (VDD), U2.131 (VDDIO2), U2.144 (VDD), U3.2 (VCC), U4.8 (VCC); also elsewhere on the board
/01-Microcontroller and Extras/BOARD_ID0: R21.1, R26.2, U2.7 (PC13)
/01-Microcontroller and Extras/BOARD_ID1: R22.1, R27.2, U2.8 (PC14)
/01-Microcontroller and Extras/BUTTON1: C6.2, R6.1, R10.2, R13.2, U2.136 (PB6)
/01-Microcontroller and Extras/BUTTON2: C7.2, R7.1, R11.2, R15.2, U2.102 (PA10)
/01-Microcontroller and Extras/BUTTON3: C8.2, R8.1, R12.2, U2.137 (PB7)
/01-Microcontroller and Extras/DEBUG_uRX_dTX: J1.10, TP11.1, U2.93 (PG8)
/01-Microcontroller and Extras/DEBUG_uTX_dRX: J1.8, TP8.1, U2.92 (PG7)
/01-Microcontroller and Extras/LED1: D1.2 (A), TP15.1, U2.123 (PD7)
/01-Microcontroller and Extras/LED2: D2.2 (A), U2.1 (PE2)
/01-Microcontroller and Extras/LED3: D3.2 (A), TP17.1, U2.9 (PC15)
/01-Microcontroller and Extras/MC_BOOT0: Q2.3 (D), R16.1, U2.138 (PH3)
/01-Microcontroller and Extras/MC_RESET_N: C30.1, J1.6, R14.1, TP6.1, U2.25 (NRST)
/01-Microcontroller and Extras/MC_SWCLK: J1.4, TP4.1, U2.109 (PA14)
/01-Microcontroller and Extras/MC_SWDIO: J1.2, TP1.1, U2.105 (PA13)
/01-Microcontroller and Extras/PC_uRX_rpiTX: R5.1, TP12.1, U2.116 (PD2)
/01-Microcontroller and Extras/PC_uTX_rpiRX: R9.1, TP13.1, U2.113 (PC12)
/01-Microcontroller and Extras/SYS_FLASH_CS_N: TP18.1, U2.86 (PD15), U4.1 (~CS)
/01-Microcontroller and Extras/SYS_IMU_CS: TP9.1, U1.12 (CS), U2.90 (PG5)
/01-Microcontroller and Extras/SYS_IMU_IRQ1: R3.1, TP2.1, U1.4 (INT1), U2.74 (PB13)
/01-Microcontroller and Extras/SYS_IMU_IRQ2: R4.1, TP5.1, U1.9 (INT2), U2.73 (PB12)
/01-Microcontroller and Extras/SYS_SPI_CLK: TP10.1, U1.13 (SCL), U2.87 (PG2), U4.6 (SCK)
/01-Microcontroller and Extras/SYS_SPI_MISO: TP3.1, U1.1 (SDO/SA0), U2.88 (PG3), U4.5 (DI(IO0))
/01-Microcontroller and Extras/SYS_SPI_MOSI: TP7.1, U1.14 (SDA), U2.89 (PG4), U4.2 (DO(IO1))
/01-Microcontroller and Extras/XTAL_IN: C22.1, U2.23 (PH0), Y2.3
/01-Microcontroller and Extras/XTAL_OUT: C21.1, U2.24 (PH1), Y2.1
ADD_LED_RGB: U2.20 (PF8); also elsewhere on the board
BM_NIRQ: U2.80 (PD11); also elsewhere on the board
INPUT1_PIN1_CURRENT_ENABLE: U2.114 (PD0); also elsewhere on the board
INPUT1_PIN1_SENSE_VOLTAGE: U2.21 (PF9); also elsewhere on the board
INPUT1_PIN2_DETECT: U2.117 (PD3); also elsewhere on the board
INPUT1_PIN5_SCL_uTX_pRX: U2.69 (PB10); also elsewhere on the board
INPUT1_PIN6_ENABLE_N: U2.115 (PD1); also elsewhere on the board
INPUT1_PIN6_SDA_uRX_pTX: U2.70 (PB11); also elsewhere on the board
INPUT1_PIN6_SENSE_VOLTAGE: U2.22 (PF10); also elsewhere on the board
INPUT2_PIN1_CURRENT_ENABLE: U2.126 (PG11); also elsewhere on the board
INPUT2_PIN1_SENSE_VOLTAGE: U2.35 (PA1); also elsewhere on the board
INPUT2_PIN2_DETECT: U2.118 (PD4); also elsewhere on the board
INPUT2_PIN5_SCL_uTX_pRX: U2.111 (PC10), U2.129 (PG14); also elsewhere on the board
INPUT2_PIN6_ENABLE_N: U2.127 (PG12); also elsewhere on the board
INPUT2_PIN6_SDA_uRX_pTX: U2.112 (PC11), U2.128 (PG13); also elsewhere on the board
INPUT2_PIN6_SENSE_VOLTAGE: U2.34 (PA0); also elsewhere on the board
INPUT3_PIN1_CURRENT_ENABLE: U2.132 (PG15); also elsewhere on the board
INPUT3_PIN1_SENSE_VOLTAGE: U2.36 (PA2); also elsewhere on the board
INPUT3_PIN2_DETECT: U2.134 (PB4); also elsewhere on the board
INPUT3_PIN5_SCL_uTX_pRX: U2.11 (PF1), U2.119 (PD5); also elsewhere on the board
INPUT3_PIN6_ENABLE_N: U2.135 (PB5); also elsewhere on the board
INPUT3_PIN6_SDA_uRX_pTX: U2.10 (PF0), U2.122 (PD6); also elsewhere on the board
INPUT3_PIN6_SENSE_VOLTAGE: U2.40 (PA4); also elsewhere on the board
INPUT4_PIN1_CURRENT_ENABLE: U2.142 (PE1); also elsewhere on the board
INPUT4_PIN2_DETECT: U2.140 (PB9); also elsewhere on the board
INPUT4_PIN5_SCL_uTX_pRX: U2.124 (PG9); also elsewhere on the board
INPUT4_PIN6_ENABLE_N: U2.139 (PB8); also elsewhere on the board
INPUT4_PIN6_SDA_uRX_pTX: U2.125 (PG10); also elsewhere on the board
INPUT4_PIN6_SENSE_VOLTAGE: U2.41 (PA5); also elsewhere on the board
MOTORAB_FAULT_N: U2.78 (PD9); also elsewhere on the board
MOTORAB_SLEEP_N: U2.77 (PD8); also elsewhere on the board
MOTORA_PIN5_ENCODER: U2.82 (PD13); also elsewhere on the board
MOTORA_PIN6_DET: U2.68 (PE15); also elsewhere on the board
MOTORA_PIN6_ENCODER: U2.81 (PD12); also elsewhere on the board
MOTORA_PWM1: U2.99 (PC9); also elsewhere on the board
MOTORA_PWM2: U2.98 (PC8); also elsewhere on the board
MOTORB_PIN6_ENCODER: U2.3 (PE4); also elsewhere on the board
MOTORB_PWM1: U2.96 (PC6); also elsewhere on the board
MOTORB_PWM2: U2.97 (PC7); also elsewhere on the board
MOTORCD_FAULT_N: U2.55 (PF15)
MOTORCD_SLEEP_N: U2.54 (PF14); also elsewhere on the board
MOTORC_PIN5_DET: U2.53 (PF13); also elsewhere on the board
MOTORC_PIN6_DET: U2.48 (PB2); also elsewhere on the board
MOTORC_PWM1: U2.67 (PE14); also elsewhere on the board
MOTORC_PWM2: U2.66 (PE13); also elsewhere on the board
MOTORD_PIN5_DET: U2.50 (PF12); also elsewhere on the board
MOTORD_PIN6_DET: U2.49 (PF11); also elsewhere on the board
MOTORD_PWM1: U2.100 (PA8); also elsewhere on the board
MOTORD_PWM2: U2.101 (PA9); also elsewhere on the board
unnamed: D1.1 (K), R23.2
unnamed: D2.1 (K), R24.2
unnamed: D3.1 (K), R25.2
unnamed: J2.8 (GPIO14/TXD), R5.2
unnamed: J2.10 (GPIO15/RXD), R9.2
unnamed: Q1.3 (D), Q2.2 (S)
unnamed: Q1.1 (G), R13.1
unnamed: Q2.1 (G), R15.1
unnamed: R11.1, SW1.2
unnamed: R12.1, SW2.2
unnamed: R1.1, U1.3 (SCX)
unnamed: R2.1, U1.2 (SDX)
unnamed: TP132.1, U2.12 (PF2)
unnamed: R17.1, U4.7 (~HOLD)
unnamed: R18.1, U4.3 (~WP)
PIEZO_PWM: U2.141 (PE0); also elsewhere on the board
PM_NIRQ: U2.85 (PD14); also elsewhere on the board
SHUTDOWN: U2.79 (PD10); also elsewhere on the board
SYS_I2C_SCL: R19.1, U2.26 (PC0), U3.3 (SCL); also elsewhere on the board
SYS_I2C_SDA: R20.1, U2.27 (PC1), U3.4 (SDA); also elsewhere on the board
USB_DN: U2.103 (PA11); also elsewhere on the board
USB_DP: U2.104 (PA12); also elsewhere on the board
VBAT_ADC_ON: U2.91 (PG6); also elsewhere on the board
VBAT_SENSE: U2.18 (PF6); also elsewhere on the board
VBUS_SENSE: U2.19 (PF7); also elsewhere on the board

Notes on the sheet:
Interruptions PD11 - BM-IRQ PB12 - IMU1 PB13 - IMU2 PD14 - PM-IRQ
TIM15_CH1
I2C3_SDA
TIM2_CH1
Close to connector
Buttons
Display OLED Module 0.96"
GPIO
ADC1_IN16
ADC1_IN13
UART1_RX
UART2_RX
ADC1_IN3
ADC3_IN7
TIM1_CH4
Address: 0x3C - 0b0111 010x
TIM8_CH1
TIM8_CH3
Close to VDD
Close to RPI Connector
USART3_TX/I2C4_SCL
External Flash
UART5_TX
TIM1_CH3
Close to VUSB
UART2_TX
DNI
I2C2_SCL
ADC1_IN5
UART5_RX
LPUART1_TX
ADC1_IN10
W25Q16JVSSIQ
Boot Control
FS_DP
USART3_RX/I2C4_SDA
TIM8_CH2
SPI1_CLK
UART4_RX
I2C3_SCL

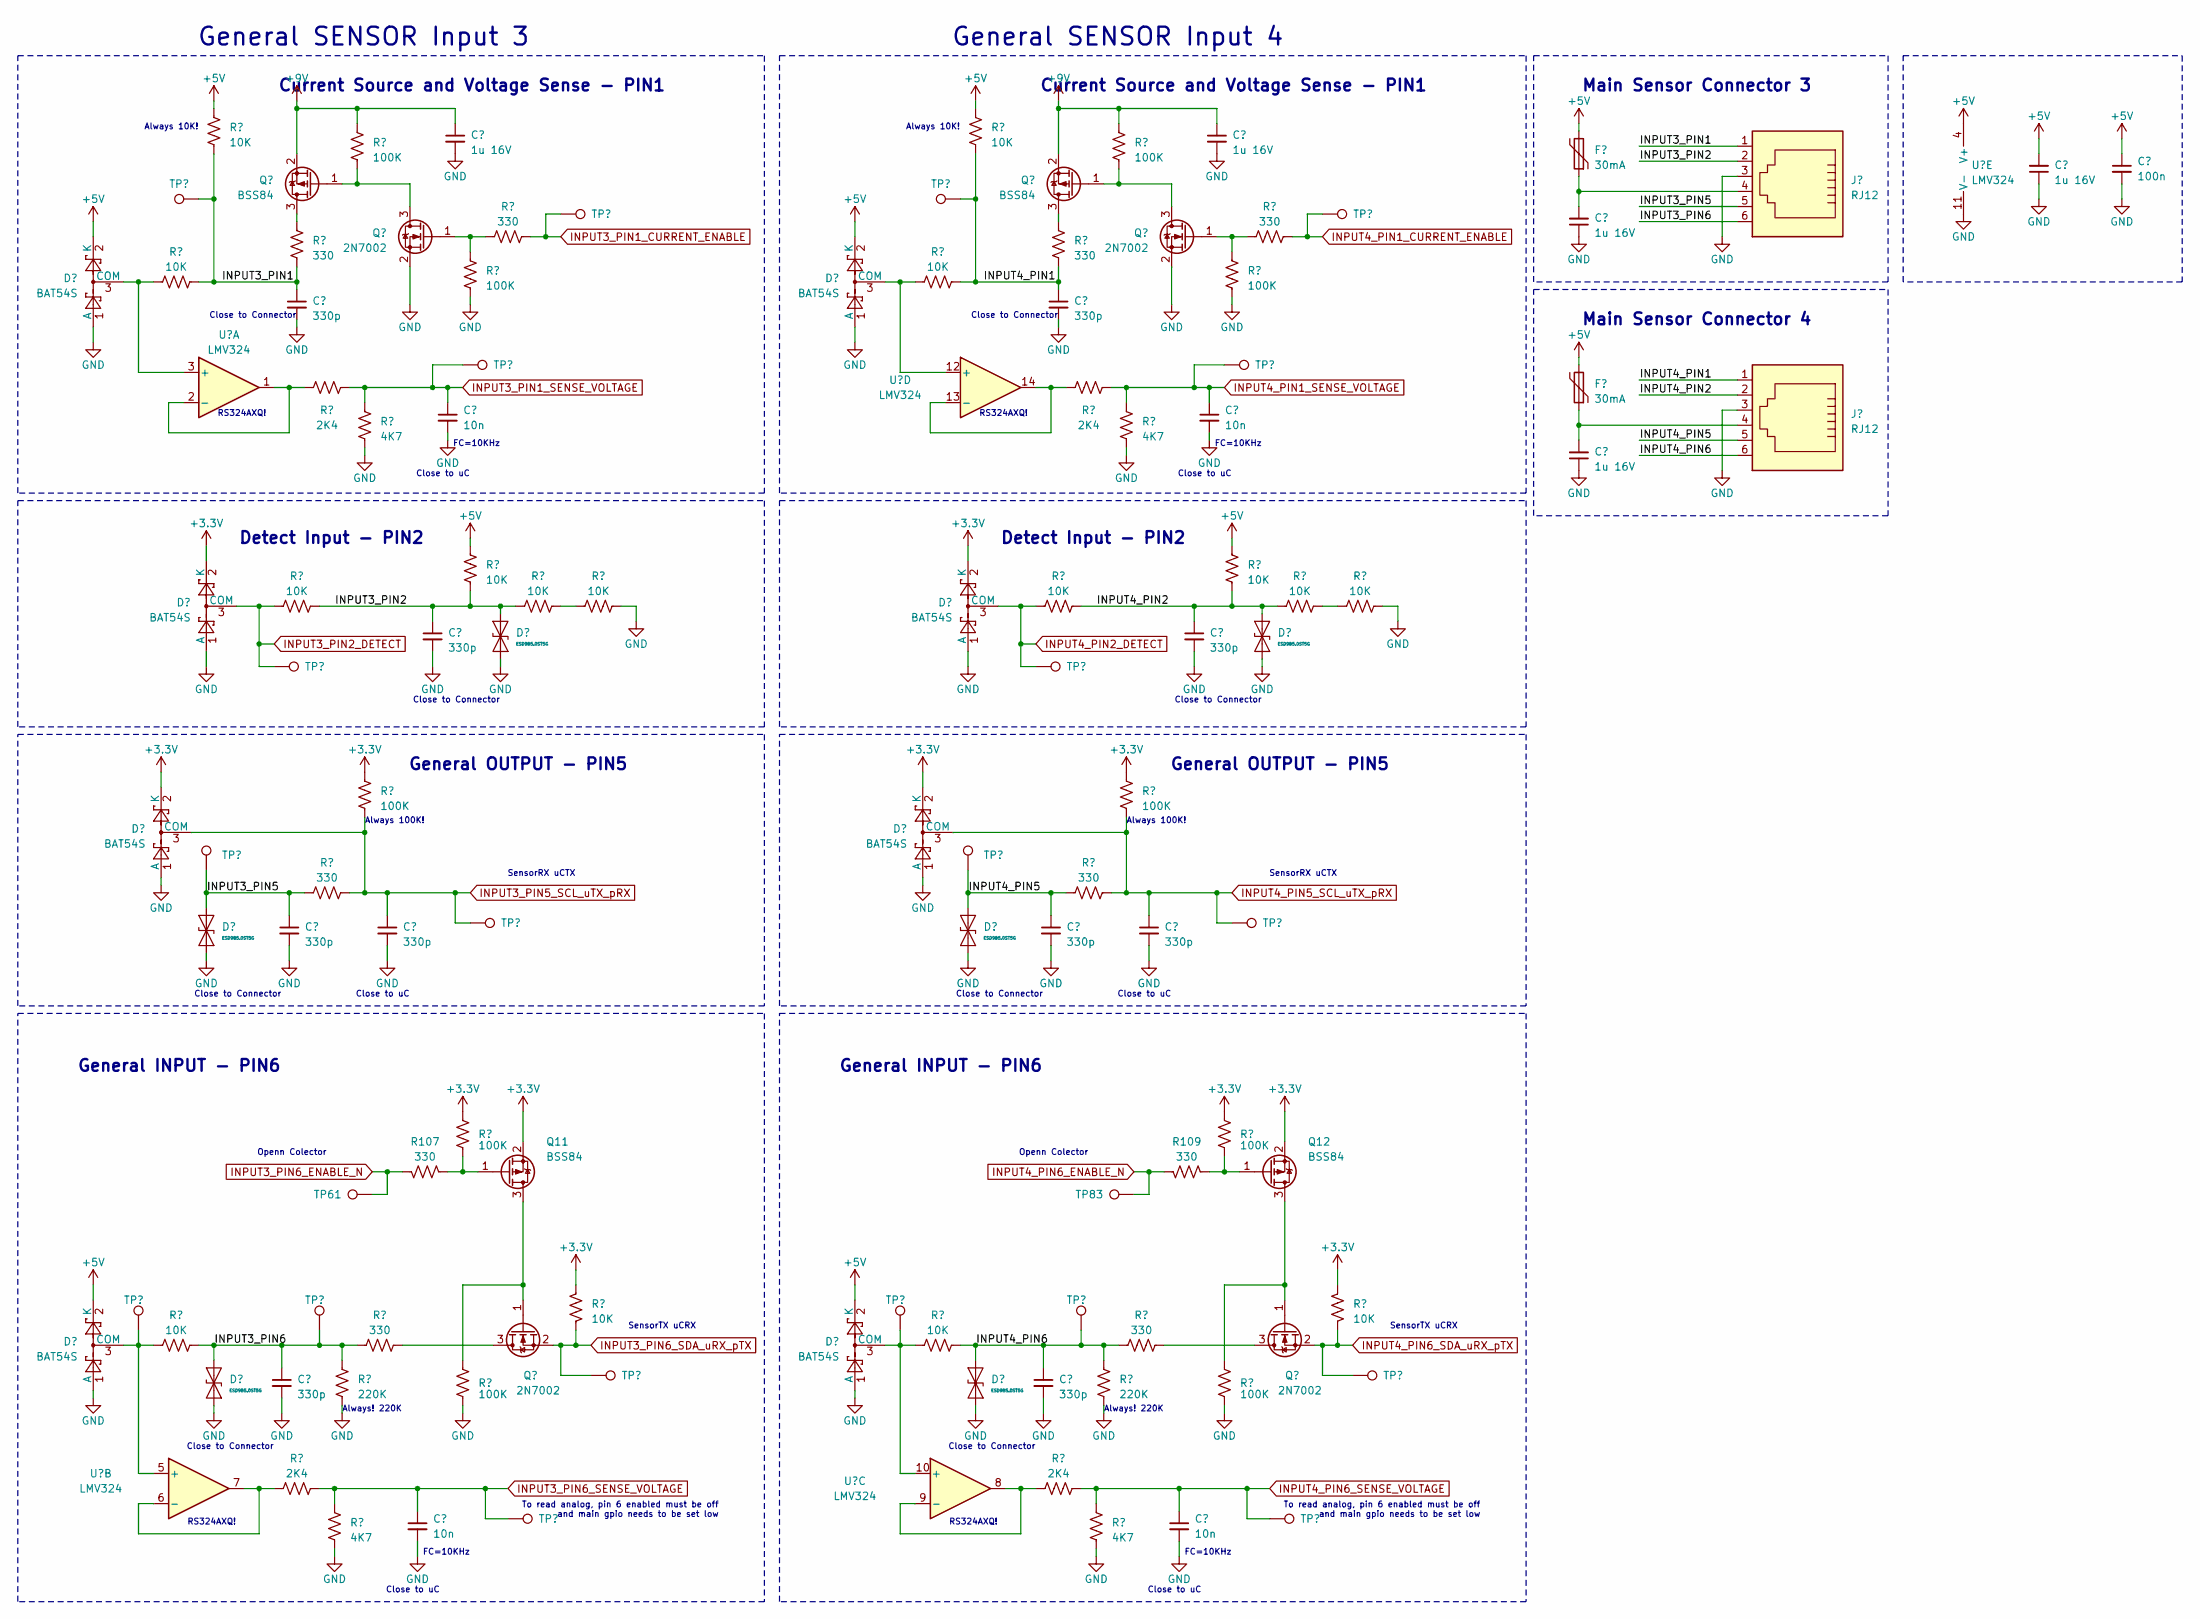
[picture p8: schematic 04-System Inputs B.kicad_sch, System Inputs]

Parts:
C110, C111, C112, C114, C119: 1u 16V; C_0603_1608Metric
C113: 100n; C_0402_1005Metric
C115, C116, C120, C121, C122, C123, C124, C125, C126, C127: 330p; C_0402_1005Metric
C117, C118, C128, C129: 10n; C_0402_1005Metric
D27, D28, D29, D30, D33, D34, D37, D38: BAT54S; SOT-23
D31, D32, D35, D36, D39, D40: ESD9B5.0ST5G; D_SOD-923
F5, F6: 30mA; R_0603_1608Metric
J9, J10: RJ12; RJ12_Amphenol_54601
Q11, Q12, Q17, Q18: BSS84; SOT-23
Q19, Q20, Q27, Q28: 2N7002; SOT-23
R106, R108, R126, R127, R132, R133, R148, R149, R167, R169: 100K; R_0402_1005Metric
R107, R109, R128, R129, R130, R131, R150, R151, R163, R165: 330; R_0402_1005Metric
R124, R125, R134, R135, R140, R141, R142, R143, R144, R145, R146, R147, R160, R161, R162, R164: 10K; R_0402_1005Metric
R136, R137, R170, R171: 2K4; R_0402_1005Metric
R138, R139, R172, R173: 4K7; R_0402_1005Metric
R166, R168: 220K; R_0402_1005Metric
TP61, TP70, TP71, TP72, TP73, TP74, TP75, TP76, TP77, TP78, TP79, TP80, TP81, TP83, TP86, TP87, TP88, TP89, TP90, TP91, TP92, TP93: S1mm; TestPoint_Pad_1.0x1.0mm
U11: LMV324; SOIC-14_3.9x8.7mm_P1.27mm

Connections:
+3.3V: D29.2 (K), D30.2 (K), D33.2 (K), D34.2 (K), Q11.2 (S), Q12.2 (S), R106.2, R108.2, R148.2, R149.2, R160.1, R161.1; also elsewhere on the board
+9V: C110.1, C111.1, Q17.2 (S), Q18.2 (S), R126.2, R127.2; also elsewhere on the board
/04-System Inputs B/INPUT3_PIN1: C115.1, J9.1, R124.1, R130.1, R134.1, TP70.1
/04-System Inputs B/INPUT3_PIN2: C120.1, D31.2 (A2), J9.2, R140.1, R142.2, R143.2
/04-System Inputs B/INPUT3_PIN5: C122.1, D35.2 (A2), J9.5, R150.2, TP78.1
/04-System Inputs B/INPUT3_PIN6: C126.1, D39.2 (A2), J9.6, R162.2, R163.2, R166.1, TP87.1
/04-System Inputs B/INPUT4_PIN1: C116.1, J10.1, R125.1, R131.1, R135.1, TP71.1
/04-System Inputs B/INPUT4_PIN2: C121.1, D32.2 (A2), J10.2, R141.1, R145.2, R146.2
/04-System Inputs B/INPUT4_PIN5: C124.1, D36.2 (A2), J10.5, R151.2, TP79.1
INPUT3_PIN1_CURRENT_ENABLE: R128.1, TP72.1; also elsewhere on the board
INPUT3_PIN1_SENSE_VOLTAGE: C117.1, R136.2, R138.1, TP74.1; also elsewhere on the board
INPUT3_PIN2_DETECT: D29.3 (COM), R142.1, TP76.1; also elsewhere on the board
INPUT3_PIN5_SCL_uTX_pRX: C123.1, D33.3 (COM), R148.1, R150.1, TP80.1; also elsewhere on the board
INPUT3_PIN6_ENABLE_N: R107.1, TP61.1; also elsewhere on the board
INPUT3_PIN6_SDA_uRX_pTX: Q27.2 (S), R160.2, TP90.1; also elsewhere on the board
INPUT3_PIN6_SENSE_VOLTAGE: C128.1, R170.2, R172.1, TP92.1; also elsewhere on the board
INPUT4_PIN1_CURRENT_ENABLE: R129.1, TP73.1; also elsewhere on the board
INPUT4_PIN2_DETECT: D30.3 (COM), R145.1, TP77.1; also elsewhere on the board
INPUT4_PIN5_SCL_uTX_pRX: C125.1, D34.3 (COM), R149.1, R151.1, TP81.1; also elsewhere on the board
INPUT4_PIN6_ENABLE_N: R109.1, TP83.1; also elsewhere on the board
INPUT4_PIN6_SDA_uRX_pTX: Q28.2 (S), R161.2, TP91.1; also elsewhere on the board
INPUT4_PIN6_SENSE_VOLTAGE: C129.1, R171.2, R173.1, TP93.1; also elsewhere on the board
unnamed: C114.2, F5.1, J9.4
unnamed: C119.2, F6.1, J10.4
unnamed: D27.3 (COM), R134.2, U11.3 (+)
unnamed: D28.3 (COM), R135.2, U11.12 (+)
unnamed: D37.3 (COM), R162.1, TP86.1, U11.5 (+)
unnamed: D38.3 (COM), R164.1, TP88.1, U11.10 (+)
unnamed: Q11.3 (D), Q27.1 (G), R167.2
unnamed: Q11.1 (G), R106.1, R107.2
unnamed: Q12.3 (D), Q28.1 (G), R169.2
unnamed: Q12.1 (G), R108.1, R109.2
unnamed: Q17.3 (D), R130.2
unnamed: Q17.1 (G), Q19.3 (D), R126.1
unnamed: Q18.3 (D), R131.2
unnamed: Q18.1 (G), Q20.3 (D), R127.1
unnamed: Q19.1 (G), R128.2, R132.2
unnamed: Q20.1 (G), R129.2, R133.2
unnamed: Q27.3 (D), R163.1
unnamed: Q28.3 (D), R165.1
unnamed: R143.1, R144.2
unnamed: R146.1, R147.2
unnamed: R136.1, U11.1, U11.2 (-)
unnamed: R170.1, U11.6 (-), U11.7
unnamed: R171.1, U11.8, U11.9 (-)
unnamed: R137.1, U11.13 (-), U11.14

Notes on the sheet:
Always 10K!
Openn Colector
General SENSOR Input 3
General OUTPUT - PIN5
FC=10KHz
Close to uC
SensorTX uCRX
Close to Connector
RS324AXQ!
SensorRX uCTX
Current Source and Voltage Sense - PIN1
To read analog, pin 6 enabled must be off and main gpio needs to be set low
Always 100K!
General SENSOR Input 4
Detect Input - PIN2
Always! 220K
Main Sensor Connector 4
General INPUT - PIN6
Main Sensor Connector 3

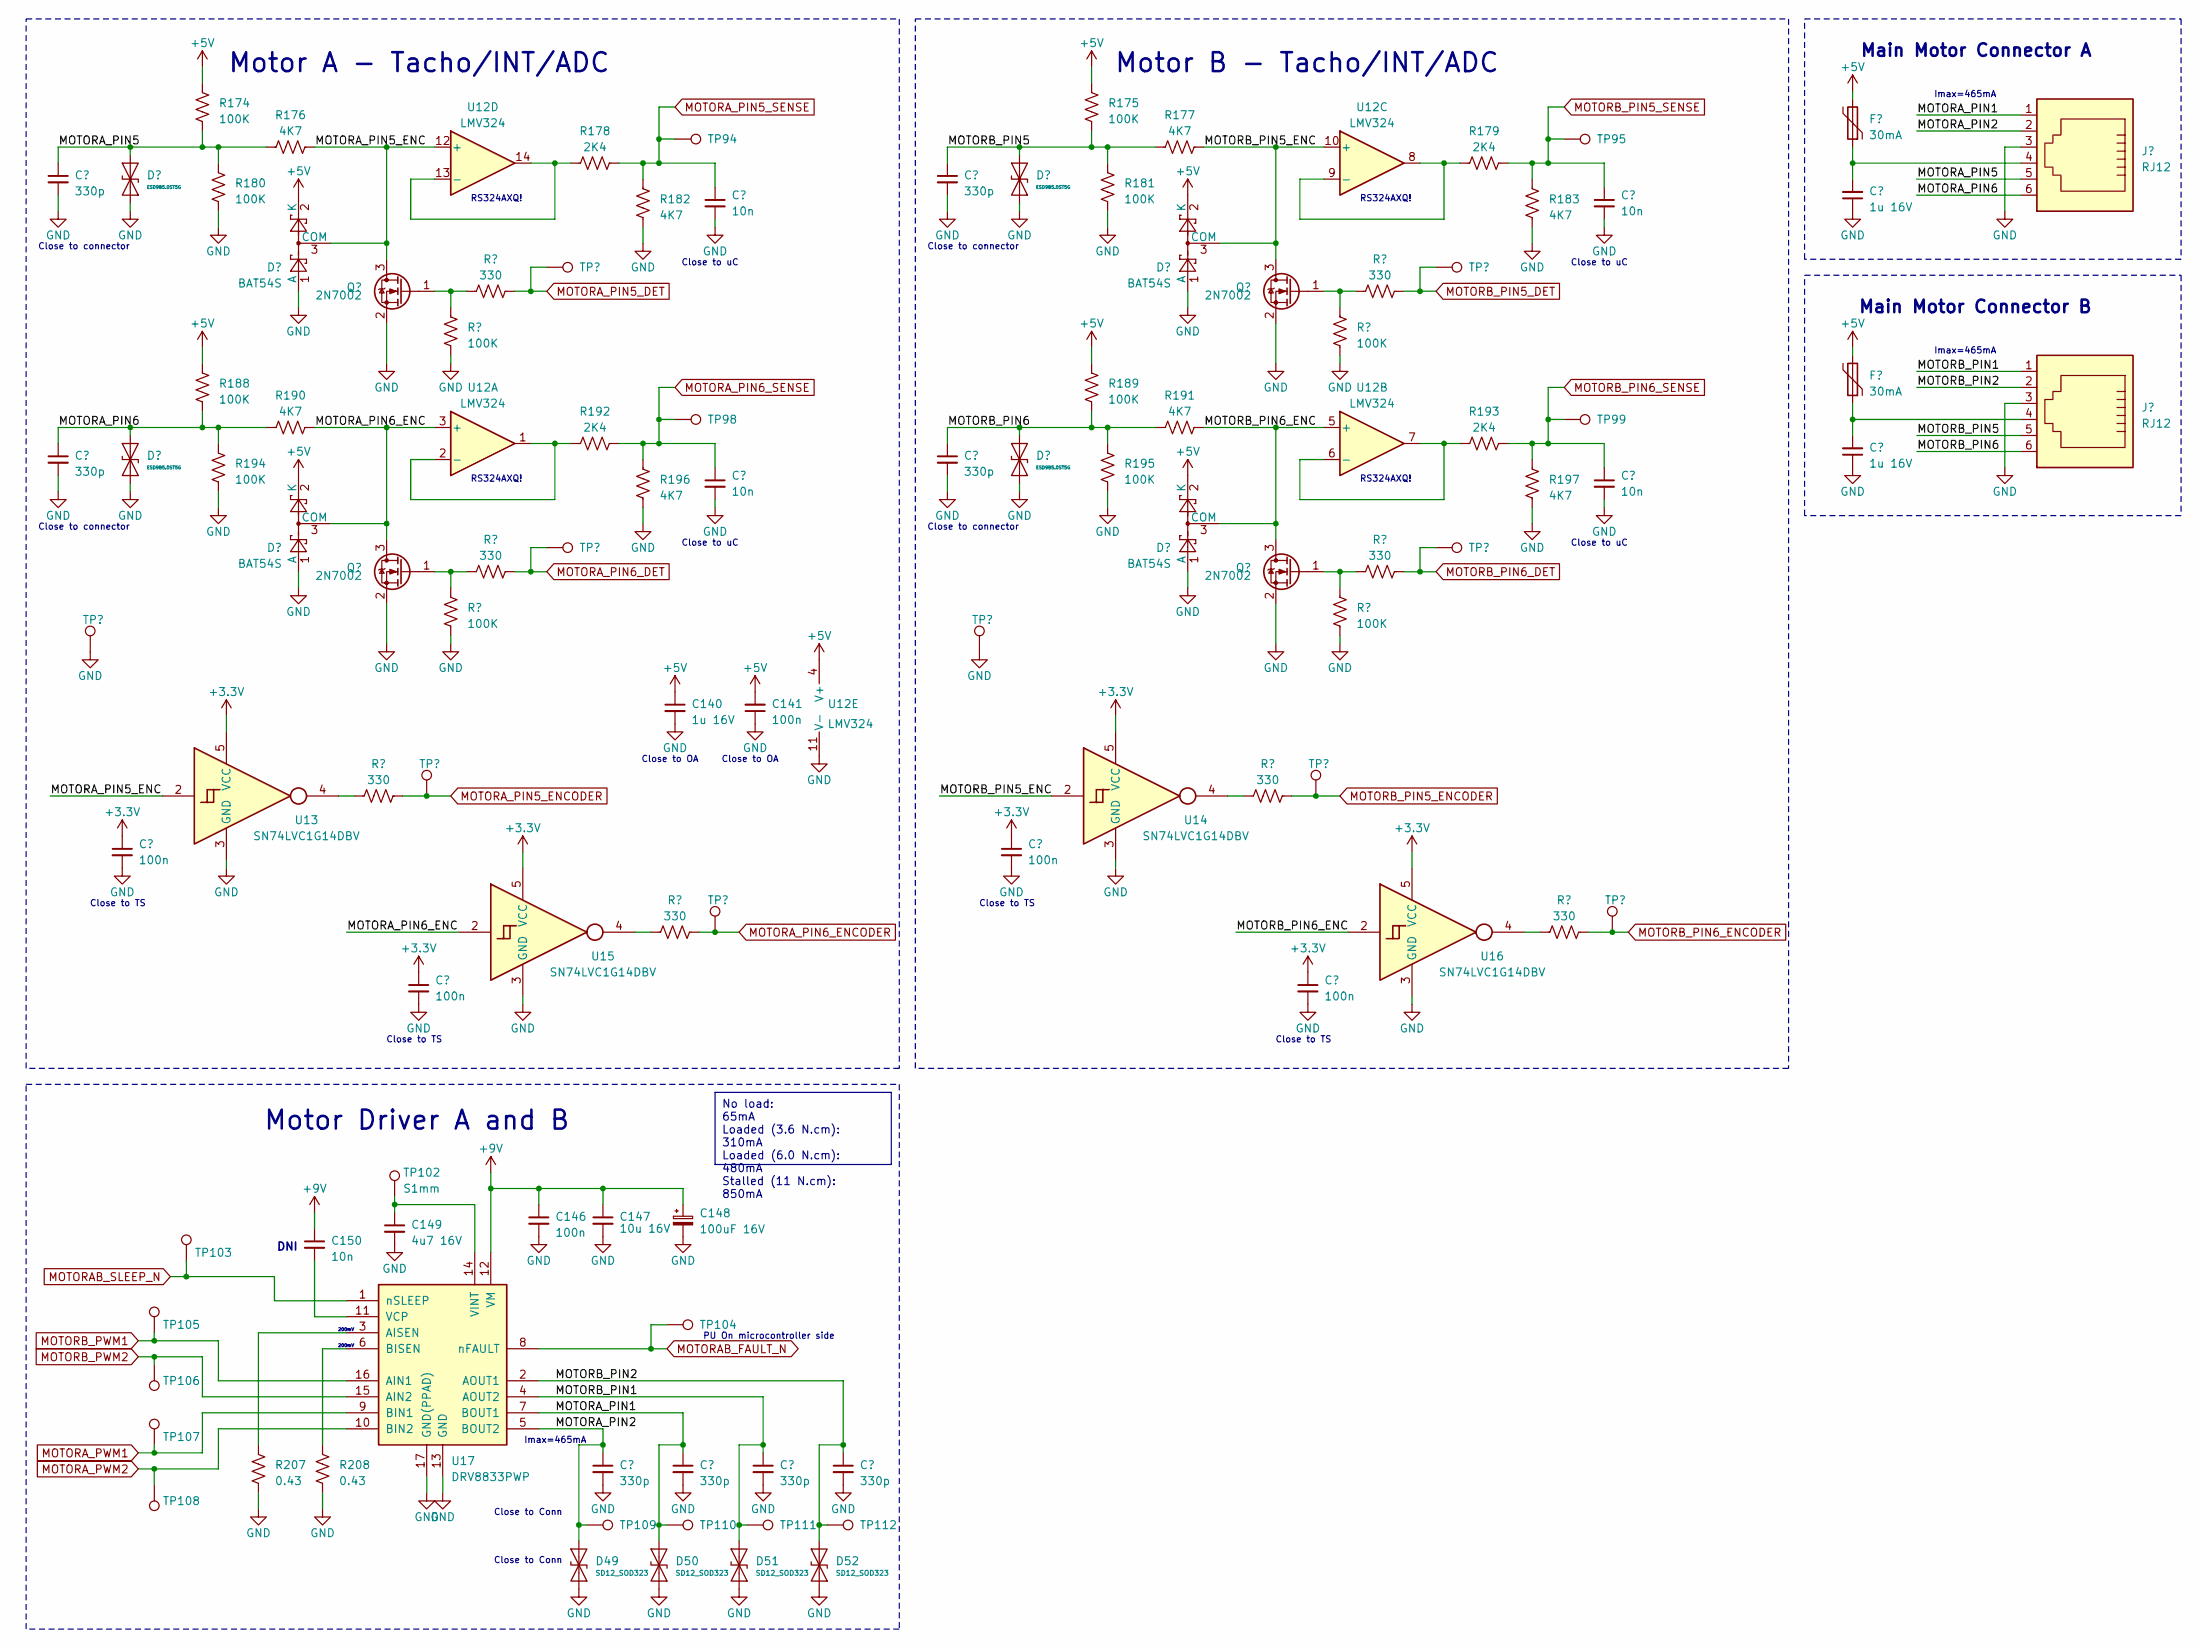
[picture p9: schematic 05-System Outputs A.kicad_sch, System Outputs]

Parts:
C118, C150: 10n; C_0402_1005Metric
C130, C131, C136, C137, C151, C152, C153, C154: 330p; C_0402_1005Metric
C132, C135, C140: 1u 16V; C_0603_1608Metric
C141, C142, C143, C144, C145, C146: 100n; C_0402_1005Metric
C147: 10u 16V; C_0805_2012Metric
C148: 100uF 16V; CP_Elec_6.3x5.2
C149: 4u7 16V; C_0603_1608Metric
D41, D42, D45, D46: ESD9B5.0ST5G; D_SOD-923
D43, D44, D47, D48: BAT54S; SOT-23
D49, D50, D51, D52: SD12_SOD323; D_SOD-323
F7, F8: 30mA; R_0603_1608Metric
J11, J12: RJ12; RJ12_Amphenol_54601
Q29, Q30, Q31, Q32: 2N7002; SOT-23
R174, R175, R180, R181, R186, R187, R188, R189, R194, R195, R200, R201: 100K; R_0402_1005Metric
R176, R177, R182, R183, R190, R191, R196, R197: 4K7; R_0402_1005Metric
R178, R179, R192, R193: 2K4; R_0402_1005Metric
R184, R185, R198, R199, R202, R203, R204, R205: 330; R_0402_1005Metric
R207, R208: 0.43; R_0805_2012Metric
TP16, TP20, TP94, TP95, TP96, TP97, TP98, TP99, TP100, TP101, TP102, TP103, TP104, TP105, TP106, TP107, TP108, TP109, TP110, TP111, TP112, TP134, TP135, TP142, TP143: S1mm; TestPoint_Pad_1.0x1.0mm
U12: LMV324; SOIC-14_3.9x8.7mm_P1.27mm
U13, U14, U15, U16: SN74LVC1G14DBV; SOT-23-5
U17: DRV8833PWP; HTSSOP-16-1EP_4.4x5mm_P0.65mm_EP3.4x5mm_Mask2.46x2.31mm_The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

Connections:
+3.3V: C142.1, C143.1, C144.1, C145.1, U13.5 (VCC), U14.5 (VCC), U15.5 (VCC), U16.5 (VCC); also elsewhere on the board
+9V: C146.1, C147.1, C148.1, C150.1, U17.12 (VM); also elsewhere on the board
/05-System Outputs A/MOTORA_PIN1: C152.1, D50.2 (A2), J11.1, TP110.1, U17.7 (BOUT1)
/05-System Outputs A/MOTORA_PIN2: C151.1, D49.2 (A2), J11.2, TP109.1, U17.5 (BOUT2)
/05-System Outputs A/MOTORA_PIN5: C130.1, D41.2 (A2), J11.5, R174.1, R176.2, R180.2
/05-System Outputs A/MOTORA_PIN5_ENC: D43.3 (COM), Q29.3 (D), R176.1, U12.12 (+), U13.2
/05-System Outputs A/MOTORA_PIN6: C136.1, D45.2 (A2), J11.6, R188.1, R190.2, R194.2
/05-System Outputs A/MOTORA_PIN6_ENC: D47.3 (COM), Q31.3 (D), R190.1, U12.3 (+), U15.2
/05-System Outputs A/MOTORB_PIN1: C153.1, D51.2 (A2), J12.1, TP111.1, U17.4 (AOUT2)
/05-System Outputs A/MOTORB_PIN2: C154.1, D52.2 (A2), J12.2, TP112.1, U17.2 (AOUT1)
/05-System Outputs A/MOTORB_PIN5: C131.1, D42.2 (A2), J12.5, R175.1, R177.2, R181.2
/05-System Outputs A/MOTORB_PIN5_ENC: D44.3 (COM), Q30.3 (D), R177.1, U12.10 (+), U14.2
/05-System Outputs A/MOTORB_PIN6: C137.1, D46.2 (A2), J12.6, R189.1, R191.2, R195.2
/05-System Outputs A/MOTORB_PIN6_ENC: D48.3 (COM), Q32.3 (D), R191.1, U12.5 (+), U16.2
MOTORAB_FAULT_N: TP104.1, U17.8 (nFAULT); also elsewhere on the board
MOTORAB_SLEEP_N: TP103.1, U17.1 (nSLEEP); also elsewhere on the board
MOTORA_PIN5_DET: R184.1, TP96.1
MOTORA_PIN5_ENCODER: R202.1, TP134.1; also elsewhere on the board
MOTORA_PIN6_DET: R198.1, TP100.1; also elsewhere on the board
MOTORA_PIN6_ENCODER: R204.1, TP135.1; also elsewhere on the board
MOTORA_PWM1: TP107.1, U17.9 (BIN1); also elsewhere on the board
MOTORA_PWM2: TP108.1, U17.10 (BIN2); also elsewhere on the board
MOTORB_PIN5_DET: R185.1, TP97.1
MOTORB_PIN6_DET: R199.1, TP101.1
MOTORB_PIN6_ENCODER: R205.1, TP20.1; also elsewhere on the board
MOTORB_PWM1: TP105.1, U17.16 (AIN1); also elsewhere on the board
MOTORB_PWM2: TP106.1, U17.15 (AIN2); also elsewhere on the board
unnamed: C132.2, F7.1, J11.4
unnamed: C135.2, F8.1, J12.4
unnamed: Q29.1 (G), R184.2, R186.2
unnamed: Q30.1 (G), R185.2, R187.2
unnamed: Q31.1 (G), R198.2, R200.2
unnamed: Q32.1 (G), R199.2, R201.2
unnamed: R202.2, U13.4
unnamed: R203.2, U14.4
unnamed: R204.2, U15.4
unnamed: R205.2, U16.4
unnamed: R192.1, U12.1, U12.2 (-)
unnamed: R193.1, U12.6 (-), U12.7
unnamed: R179.1, U12.8, U12.9 (-)
unnamed: R178.1, U12.13 (-), U12.14
unnamed: R207.2, U17.3 (AISEN)
unnamed: R208.2, U17.6 (BISEN)
unnamed: C150.2, U17.11 (VCP)
unnamed: C149.1, TP102.1, U17.14 (VINT)

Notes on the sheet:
No load: 65mA Loaded (3.6 N.cm): 310mA Loaded (6.0 N.cm): 480mA Stalled (11 N.cm): 850mA
RS324AXQ!
Motor A - Tacho/INT/ADC
Close to connector
Close to Conn
Close to uC
200mV
Close to TS
Main Motor Connector B
Motor Driver A and B
Imax=465mA
DNI
Main Motor Connector A
PU On microcontroller side
Close to OA
Motor B - Tacho/INT/ADC

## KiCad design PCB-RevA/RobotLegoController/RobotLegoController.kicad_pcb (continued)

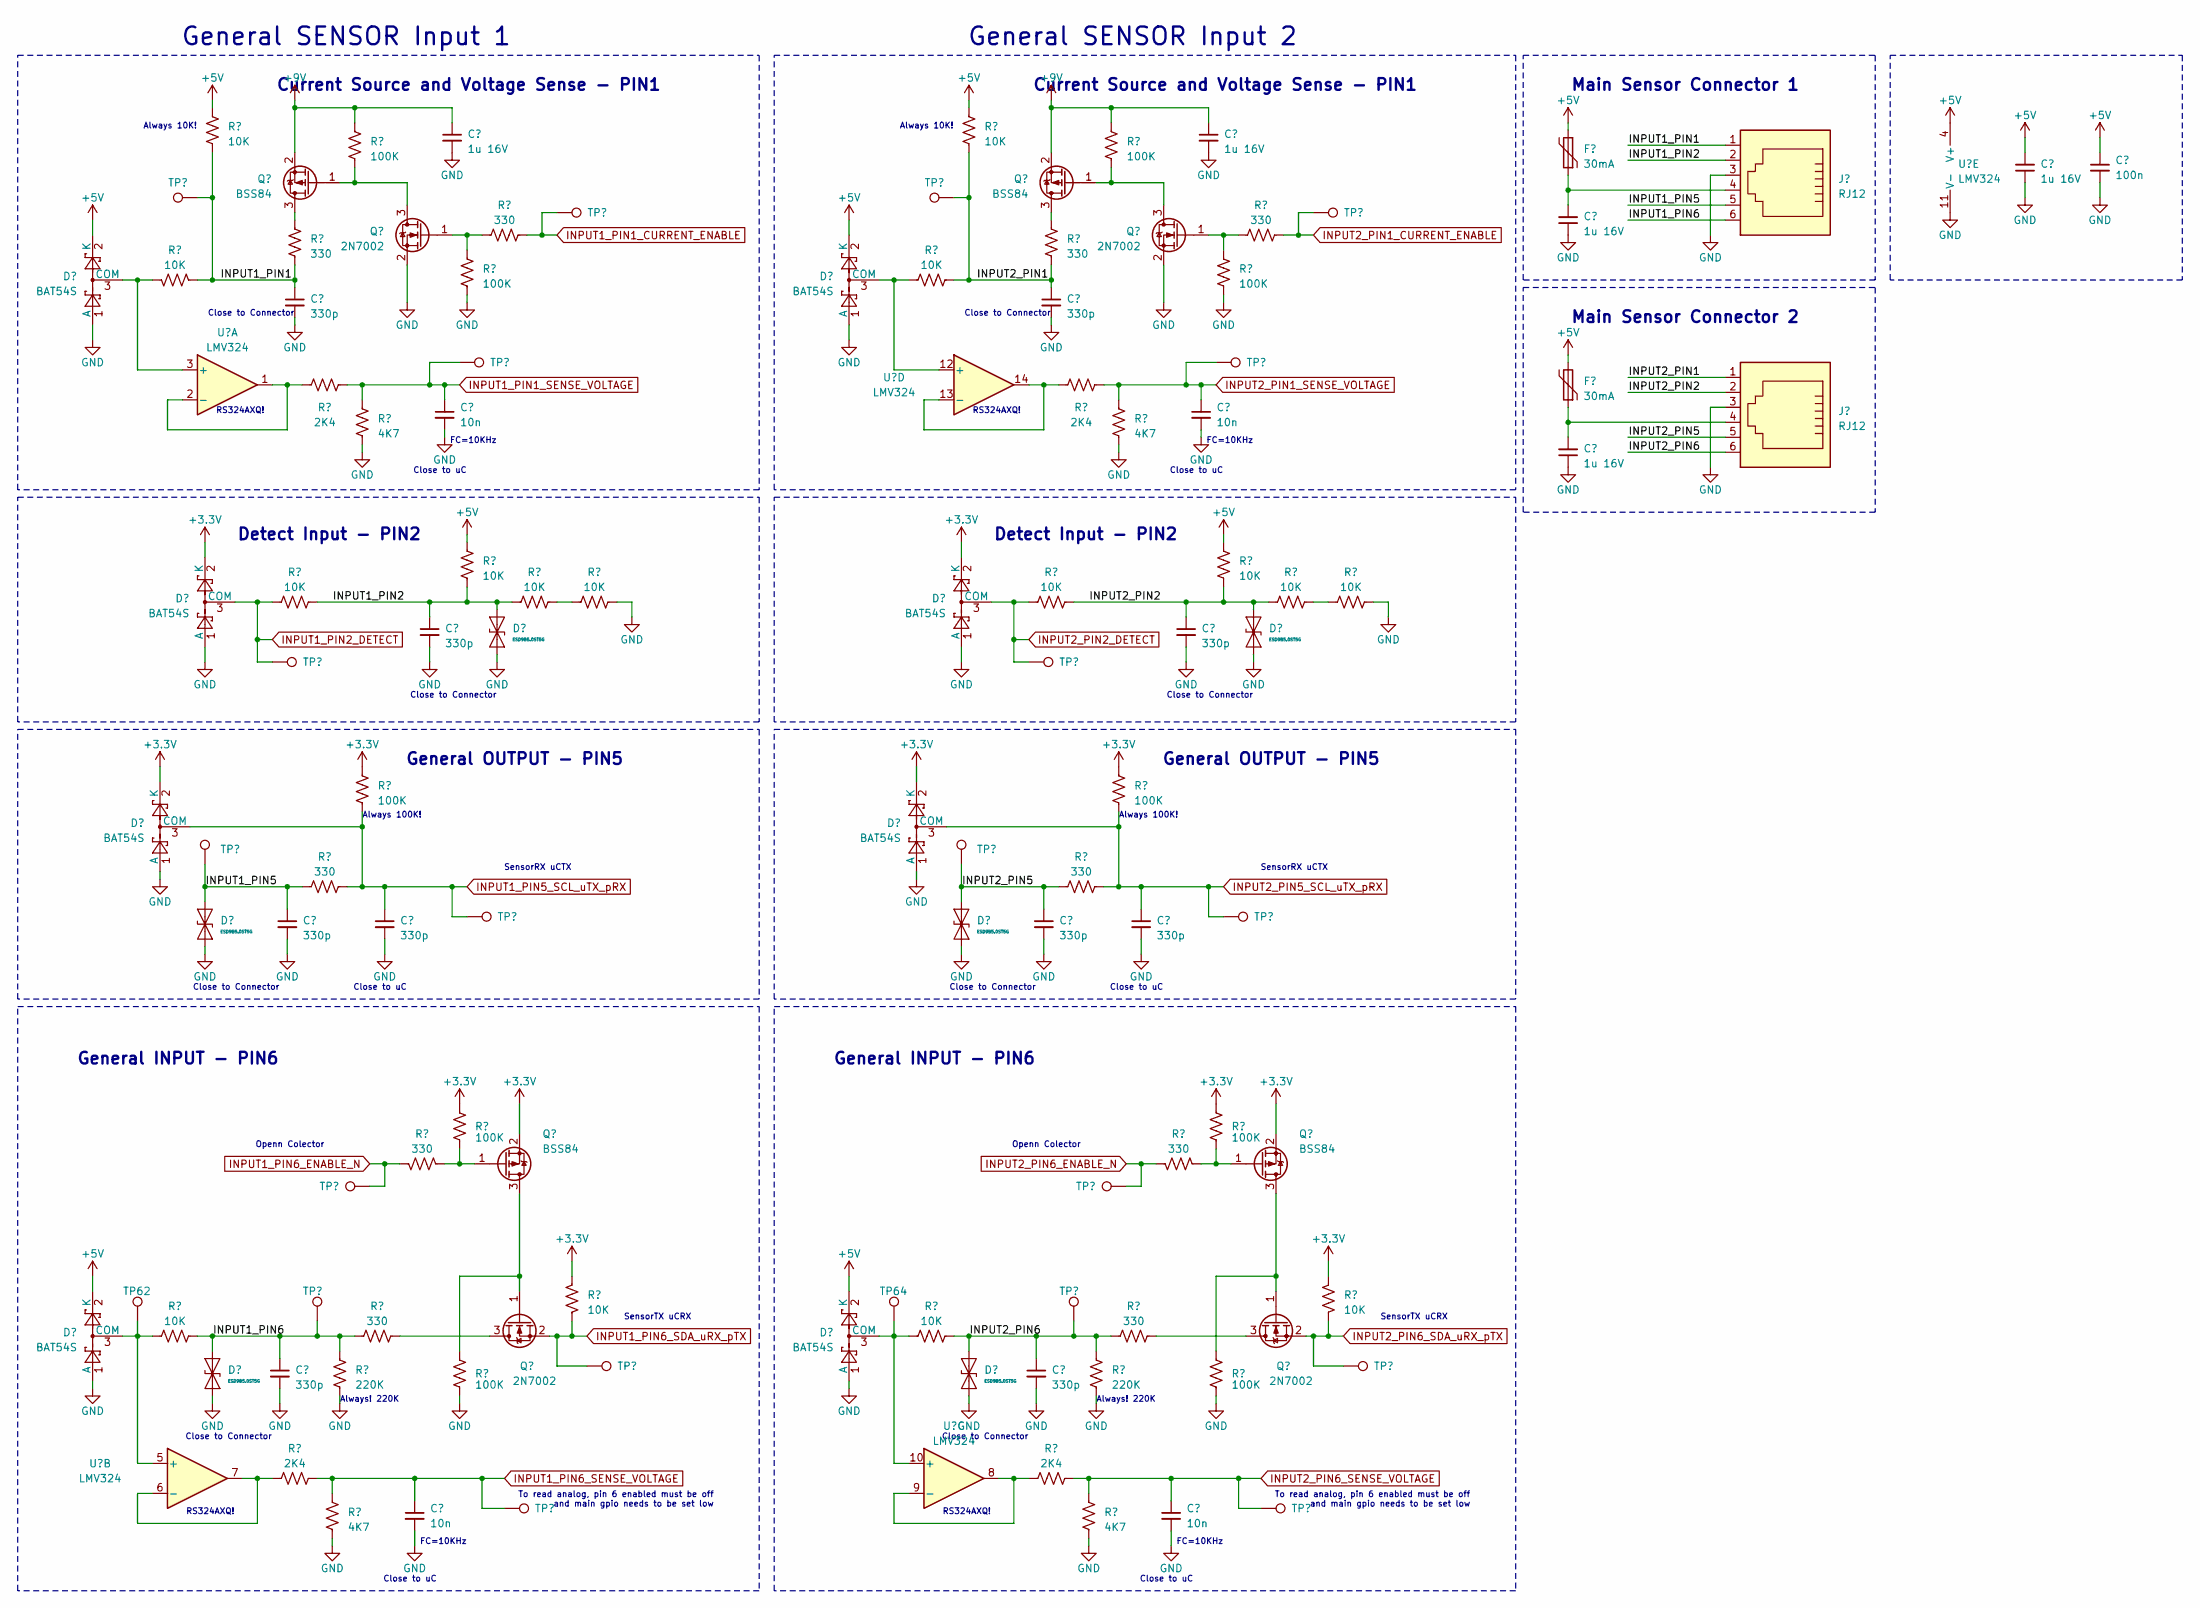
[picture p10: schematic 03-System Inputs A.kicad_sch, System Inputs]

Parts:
C90, C91, C92, C94, C99: 1u 16V; C_0603_1608Metric
C93: 100n; C_0402_1005Metric
C95, C96, C100, C101, C102, C103, C104, C105, C106, C107: 330p; C_0402_1005Metric
C97, C98, C108, C109: 10n; C_0402_1005Metric
D13, D14, D15, D16, D19, D20, D23, D24: BAT54S; SOT-23
D17, D18, D21, D22, D25, D26: ESD9B5.0ST5G; D_SOD-923
F3, F4: 30mA; R_0603_1608Metric
J7, J8: RJ12; RJ12_Amphenol_54601
Q5, Q6, Q9, Q10: BSS84; SOT-23
Q7, Q8, Q15, Q16: 2N7002; SOT-23
R74, R75, R84, R85, R90, R91, R92, R93, R94, R95, R96, R97, R110, R111, R112, R114: 10K; R_0402_1005Metric
R76, R77, R82, R83, R98, R99, R102, R103, R117, R119: 100K; R_0402_1005Metric
R78, R79, R80, R81, R100, R101, R104, R105, R113, R115: 330; R_0402_1005Metric
R86, R87, R120, R121: 2K4; R_0402_1005Metric
R88, R89, R122, R123: 4K7; R_0402_1005Metric
R116, R118: 220K; R_0402_1005Metric
TP46, TP47, TP48, TP49, TP50, TP51, TP52, TP53, TP54, TP55, TP56, TP57, TP59, TP60, TP62, TP63, TP64, TP65, TP66, TP67, TP68, TP69: S1mm; TestPoint_Pad_1.0x1.0mm
U10: LMV324; SOIC-14_3.9x8.7mm_P1.27mm

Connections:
+3.3V: D15.2 (K), D16.2 (K), D19.2 (K), D20.2 (K), Q9.2 (S), Q10.2 (S), R98.2, R99.2, R102.2, R103.2, R110.1, R111.1; also elsewhere on the board
+9V: C90.1, C91.1, Q5.2 (S), Q6.2 (S), R76.2, R77.2; also elsewhere on the board
/03-System Inputs A/INPUT1_PIN1: C95.1, J7.1, R74.1, R80.1, R84.2, TP46.1
/03-System Inputs A/INPUT1_PIN2: C100.1, D17.2 (A2), J7.2, R90.1, R92.2, R93.2
/03-System Inputs A/INPUT1_PIN5: C102.1, D21.2 (A2), J7.5, R100.2, TP54.1
/03-System Inputs A/INPUT1_PIN6: C106.1, D25.2 (A2), J7.6, R112.2, R113.2, R116.1, TP63.1
/03-System Inputs A/INPUT2_PIN1: C96.1, J8.1, R75.1, R81.1, R85.1, TP47.1
/03-System Inputs A/INPUT2_PIN2: C101.1, D18.2 (A2), J8.2, R91.1, R95.2, R96.2
/03-System Inputs A/INPUT2_PIN5: C104.1, D22.2 (A2), J8.5, R101.2, TP55.1
/03-System Inputs A/INPUT2_PIN6: C107.1, D26.2 (A2), J8.6, R114.2, R115.2, R118.1, TP65.1
INPUT1_PIN1_CURRENT_ENABLE: R78.1, TP48.1; also elsewhere on the board
INPUT1_PIN1_SENSE_VOLTAGE: C97.1, R86.2, R88.1, TP50.1; also elsewhere on the board
INPUT1_PIN2_DETECT: D15.3 (COM), R92.1, TP52.1; also elsewhere on the board
INPUT1_PIN5_SCL_uTX_pRX: C103.1, D19.3 (COM), R98.1, R100.1, TP56.1; also elsewhere on the board
INPUT1_PIN6_ENABLE_N: R104.1, TP60.1; also elsewhere on the board
INPUT1_PIN6_SDA_uRX_pTX: Q15.2 (S), R110.2, TP66.1; also elsewhere on the board
INPUT1_PIN6_SENSE_VOLTAGE: C108.1, R120.2, R122.1, TP68.1; also elsewhere on the board
INPUT2_PIN1_CURRENT_ENABLE: R79.1, TP49.1; also elsewhere on the board
INPUT2_PIN1_SENSE_VOLTAGE: C98.1, R87.2, R89.1, TP51.1; also elsewhere on the board
INPUT2_PIN2_DETECT: D16.3 (COM), R95.1, TP53.1; also elsewhere on the board
INPUT2_PIN5_SCL_uTX_pRX: C105.1, D20.3 (COM), R99.1, R101.1, TP57.1; also elsewhere on the board
INPUT2_PIN6_ENABLE_N: R105.1, TP59.1; also elsewhere on the board
INPUT2_PIN6_SDA_uRX_pTX: Q16.2 (S), R111.2, TP67.1; also elsewhere on the board
INPUT2_PIN6_SENSE_VOLTAGE: C109.1, R121.2, R123.1, TP69.1; also elsewhere on the board
unnamed: C94.2, F3.1, J7.4
unnamed: C99.2, F4.1, J8.4
unnamed: D13.3 (COM), R84.1, U10.3 (+)
unnamed: D14.3 (COM), R85.2, U10.12 (+)
unnamed: D23.3 (COM), R112.1, TP62.1, U10.5 (+)
unnamed: D24.3 (COM), R114.1, TP64.1, U10.10 (+)
unnamed: Q5.3 (D), R80.2
unnamed: Q5.1 (G), Q7.3 (D), R76.1
unnamed: Q6.3 (D), R81.2
unnamed: Q6.1 (G), Q8.3 (D), R77.1
unnamed: Q7.1 (G), R78.2, R82.2
unnamed: Q8.1 (G), R79.2, R83.2
unnamed: Q9.1 (G), R103.1, R105.2
unnamed: Q10.3 (D), Q15.1 (G), R117.2
unnamed: Q10.1 (G), R102.1, R104.2
unnamed: Q15.3 (D), R113.1
unnamed: Q16.3 (D), R115.1
unnamed: Q9.3 (D), Q16.1 (G), R119.2
unnamed: R93.1, R94.2
unnamed: R96.1, R97.2
unnamed: R86.1, U10.1, U10.2 (-)
unnamed: R120.1, U10.6 (-), U10.7
unnamed: R121.1, U10.8, U10.9 (-)
unnamed: R87.1, U10.13 (-), U10.14

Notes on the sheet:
RS324AXQ!
General OUTPUT - PIN5
Close to Connector
Main Sensor Connector 2
Close to uC
FC=10KHz
General SENSOR Input 2
Detect Input - PIN2
Main Sensor Connector 1
To read analog, pin 6 enabled must be off and main gpio needs to be set low
Openn Colector
Current Source and Voltage Sense - PIN1
Always 100K!
General SENSOR Input 1
General INPUT - PIN6
Always 10K!
SensorRX uCTX
Always! 220K
SensorTX uCRX

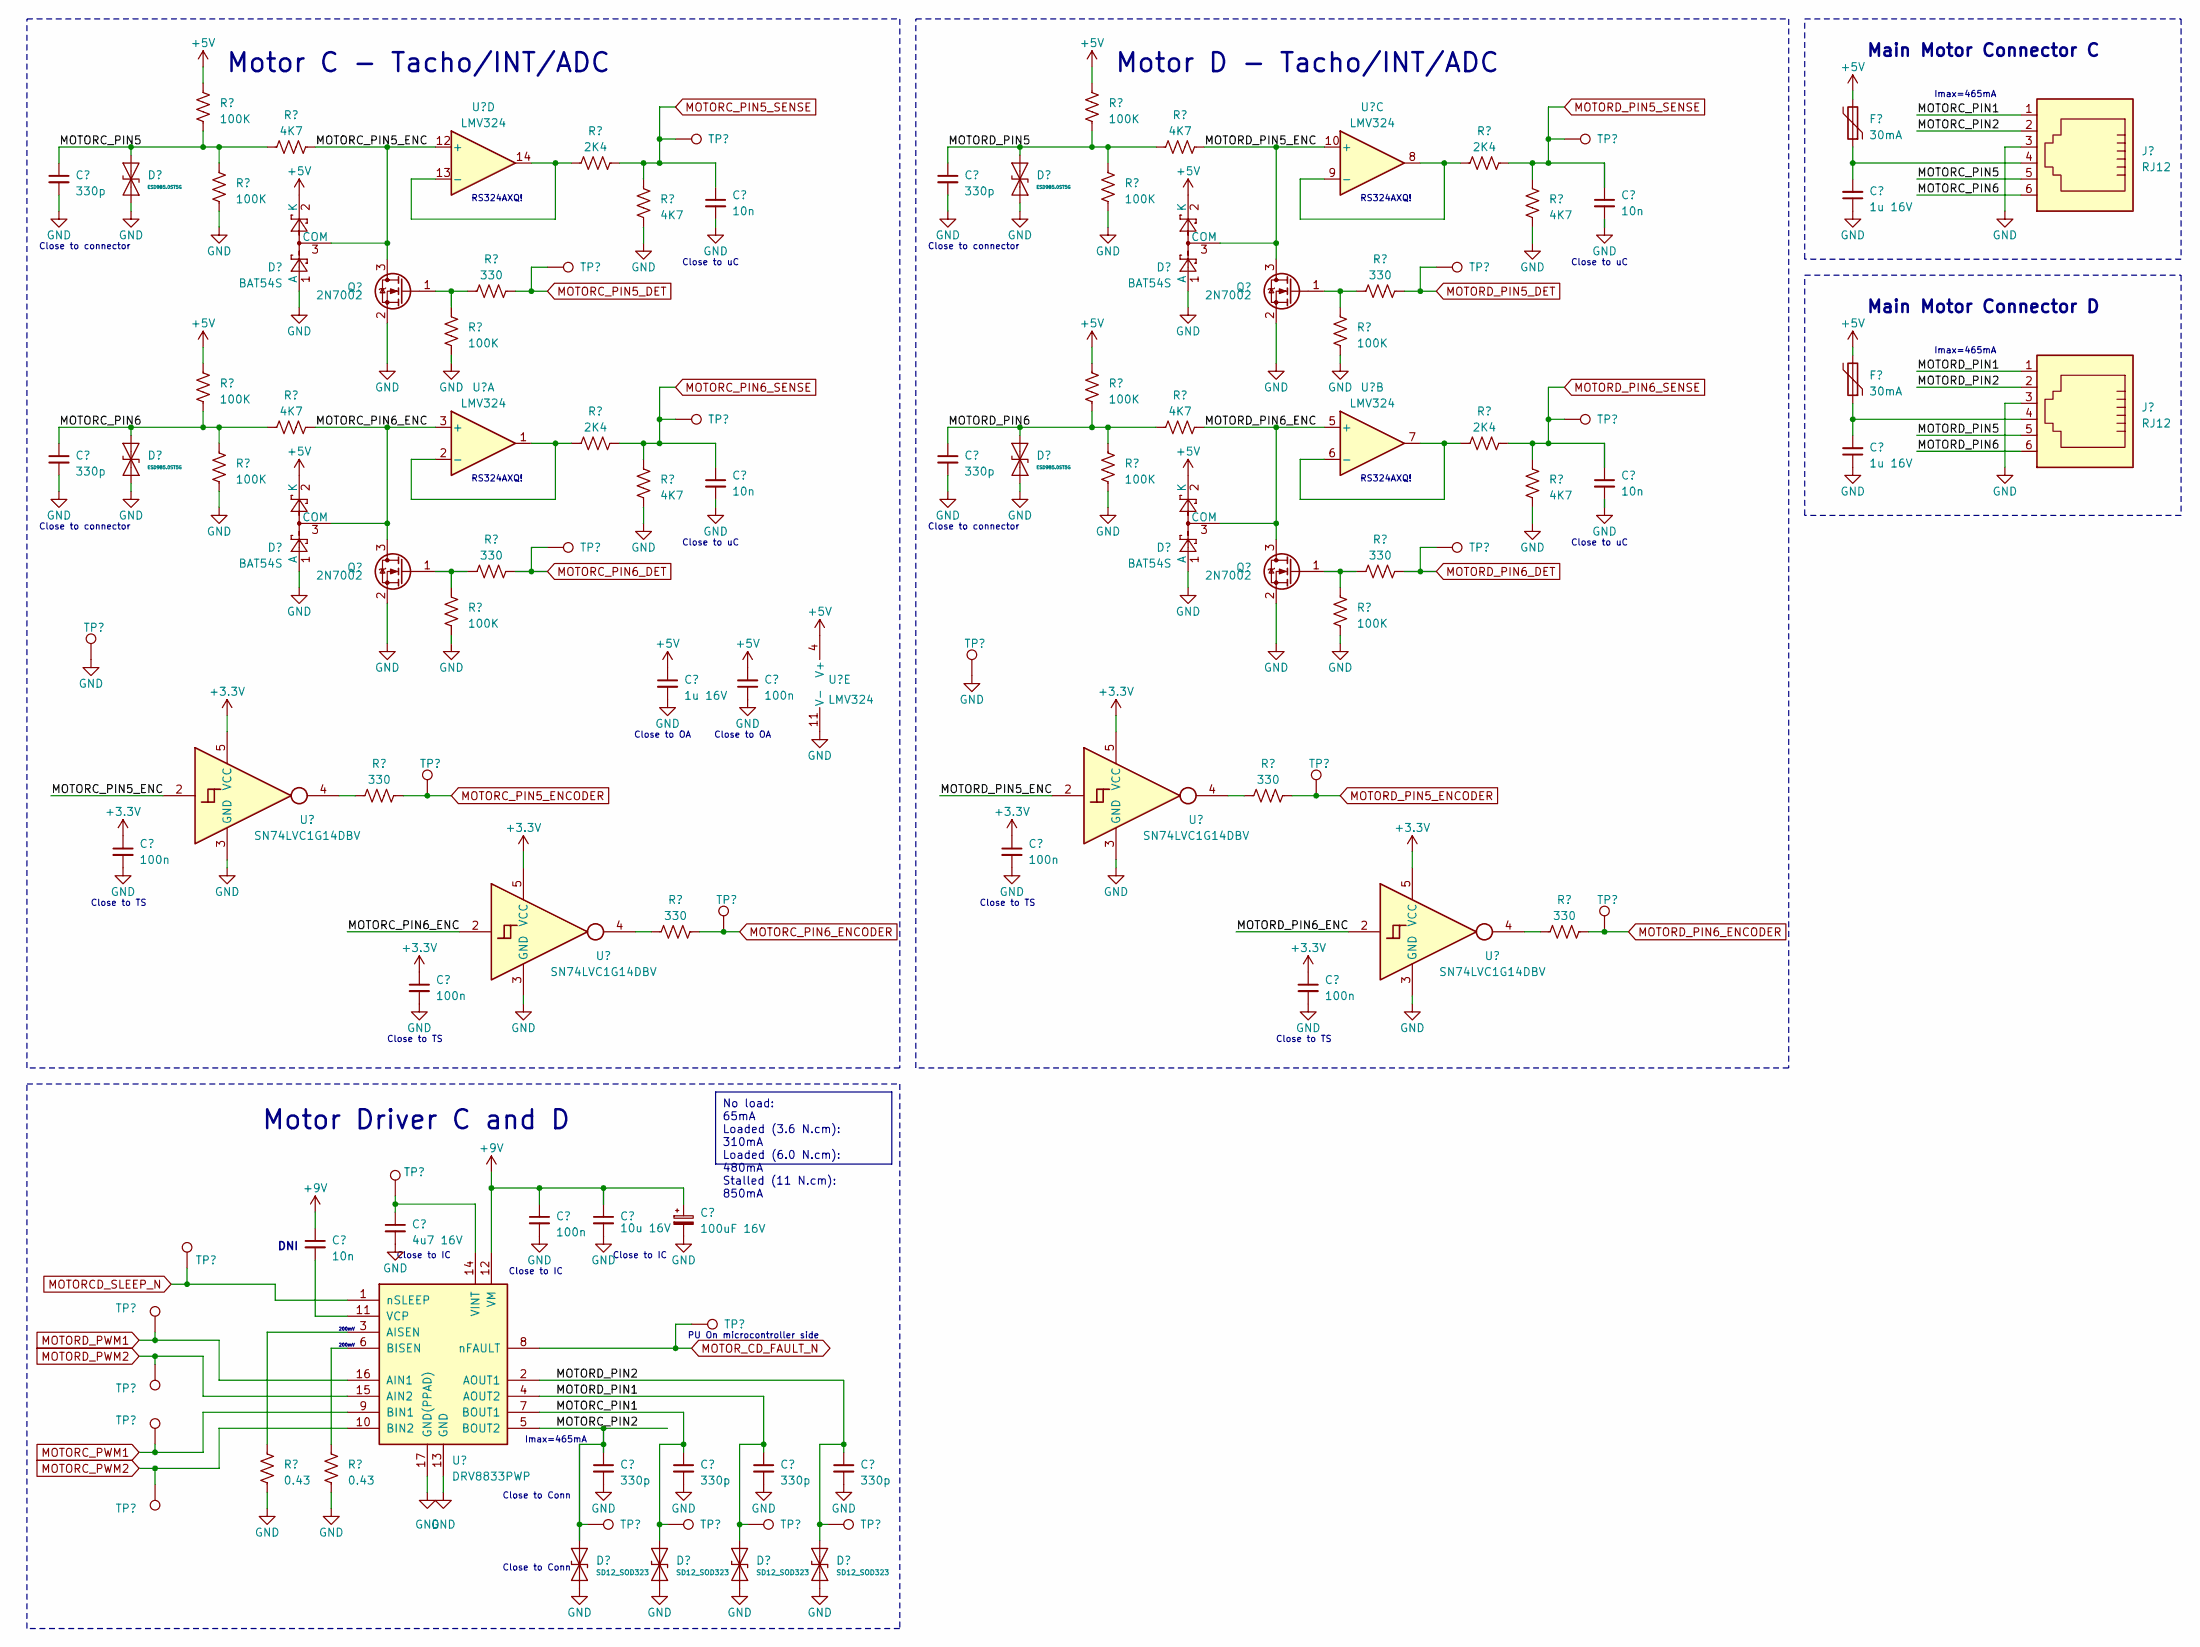
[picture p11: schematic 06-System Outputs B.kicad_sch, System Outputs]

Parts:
C118, C175: 10n; C_0402_1005Metric
C155, C156, C161, C162, C176, C177, C178, C179: 330p; C_0402_1005Metric
C157, C160, C165: 1u 16V; C_0603_1608Metric
C166, C167, C168, C169, C170, C171: 100n; C_0402_1005Metric
C172: 10u 16V; C_0805_2012Metric
C173: 100uF 16V; CP_Elec_6.3x5.2
C174: 4u7 16V; C_0603_1608Metric
D53, D54, D57, D58: ESD9B5.0ST5G; D_SOD-923
D55, D56, D59, D60: BAT54S; SOT-23
D61, D62, D63, D64: SD12_SOD323; D_SOD-323
F9, F10: 30mA; R_0603_1608Metric
J13, J14: RJ12; RJ12_Amphenol_54601
Q33, Q34, Q35, Q36: 2N7002; SOT-23
R209, R210, R215, R216, R221, R222, R223, R224, R229, R230, R235, R236: 100K; R_0402_1005Metric
R211, R212, R217, R218, R225, R226, R231, R232: 4K7; R_0402_1005Metric
R213, R214, R227, R228: 2K4; R_0402_1005Metric
R219, R220, R233, R234, R237, R238, R239, R240: 330; R_0402_1005Metric
R242, R243: 0.43; R_0805_2012Metric
TP16, TP113, TP114, TP115, TP116, TP117, TP118, TP119, TP120, TP121, TP122, TP123, TP124, TP125, TP126, TP127, TP128, TP129, TP130, TP131: S1mm; TestPoint_Pad_1.0x1.0mm
U18: LMV324; SOIC-14_3.9x8.7mm_P1.27mm
U19, U20, U21, U22: SN74LVC1G14DBV; SOT-23-5
U23: DRV8833PWP; HTSSOP-16-1EP_4.4x5mm_P0.65mm_EP3.4x5mm_Mask2.46x2.31mm_The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

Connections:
+3.3V: C167.1, C168.1, C169.1, C170.1, U19.5 (VCC), U20.5 (VCC), U21.5 (VCC), U22.5 (VCC); also elsewhere on the board
+9V: C171.1, C172.1, C173.1, C175.1, U23.12 (VM); also elsewhere on the board
/06-System Outputs B/MOTORC_PIN1: C177.1, D62.2 (A2), J13.1, TP129.1, U23.7 (BOUT1)
/06-System Outputs B/MOTORC_PIN2: C176.1, D61.2 (A2), J13.2, TP128.1, U23.5 (BOUT2)
/06-System Outputs B/MOTORC_PIN5: C155.1, D53.2 (A2), J13.5, R209.1, R211.2, R215.2
/06-System Outputs B/MOTORC_PIN5_ENC: D55.3 (COM), Q33.3 (D), R211.1, U18.12 (+), U19.2
/06-System Outputs B/MOTORC_PIN6: C161.1, D57.2 (A2), J13.6, R223.1, R225.2, R229.2
/06-System Outputs B/MOTORC_PIN6_ENC: D59.3 (COM), Q35.3 (D), R225.1, U18.3 (+), U21.2
/06-System Outputs B/MOTORD_PIN1: C178.1, D63.2 (A2), J14.1, TP130.1, U23.4 (AOUT2)
/06-System Outputs B/MOTORD_PIN2: C179.1, D64.2 (A2), J14.2, TP131.1, U23.2 (AOUT1)
/06-System Outputs B/MOTORD_PIN5: C156.1, D54.2 (A2), J14.5, R210.1, R212.2, R216.2
/06-System Outputs B/MOTORD_PIN5_ENC: D56.3 (COM), Q34.3 (D), R212.1, U18.10 (+), U20.2
/06-System Outputs B/MOTORD_PIN6: C162.1, D58.2 (A2), J14.6, R224.1, R226.2, R230.2
/06-System Outputs B/MOTORD_PIN6_ENC: D60.3 (COM), Q36.3 (D), R226.1, U18.5 (+), U22.2
MOTORCD_SLEEP_N: TP122.1, U23.1 (nSLEEP); also elsewhere on the board
MOTORC_PIN5_DET: R219.1, TP115.1; also elsewhere on the board
MOTORC_PIN6_DET: R233.1, TP119.1; also elsewhere on the board
MOTORC_PWM1: TP126.1, U23.9 (BIN1); also elsewhere on the board
MOTORC_PWM2: TP127.1, U23.10 (BIN2); also elsewhere on the board
MOTORD_PIN5_DET: R220.1, TP116.1; also elsewhere on the board
MOTORD_PIN6_DET: R234.1, TP120.1; also elsewhere on the board
MOTORD_PWM1: TP124.1, U23.16 (AIN1); also elsewhere on the board
MOTORD_PWM2: TP125.1, U23.15 (AIN2); also elsewhere on the board
MOTOR_CD_FAULT_N: TP123.1, U23.8 (nFAULT)
unnamed: C157.2, F9.1, J13.4
unnamed: C160.2, F10.1, J14.4
unnamed: Q33.1 (G), R219.2, R221.2
unnamed: Q34.1 (G), R220.2, R222.2
unnamed: Q35.1 (G), R233.2, R235.2
unnamed: Q36.1 (G), R234.2, R236.2
unnamed: R237.2, U19.4
unnamed: R238.2, U20.4
unnamed: R239.2, U21.4
unnamed: R240.2, U22.4
unnamed: R227.1, U18.1, U18.2 (-)
unnamed: R228.1, U18.6 (-), U18.7
unnamed: R214.1, U18.8, U18.9 (-)
unnamed: R213.1, U18.13 (-), U18.14
unnamed: R242.2, U23.3 (AISEN)
unnamed: R243.2, U23.6 (BISEN)
unnamed: C175.2, U23.11 (VCP)
unnamed: C174.1, TP121.1, U23.14 (VINT)

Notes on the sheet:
No load: 65mA Loaded (3.6 N.cm): 310mA Loaded (6.0 N.cm): 480mA Stalled (11 N.cm): 850mA
Close to IC
Close to TS
200mV
RS324AXQ!
Close to connector
Main Motor Connector D
Close to uC
Close to OA
Close to Conn
DNI
Motor C - Tacho/INT/ADC
Imax=465mA
Motor Driver C and D
PU On microcontroller side
Main Motor Connector C
Motor D - Tacho/INT/ADC

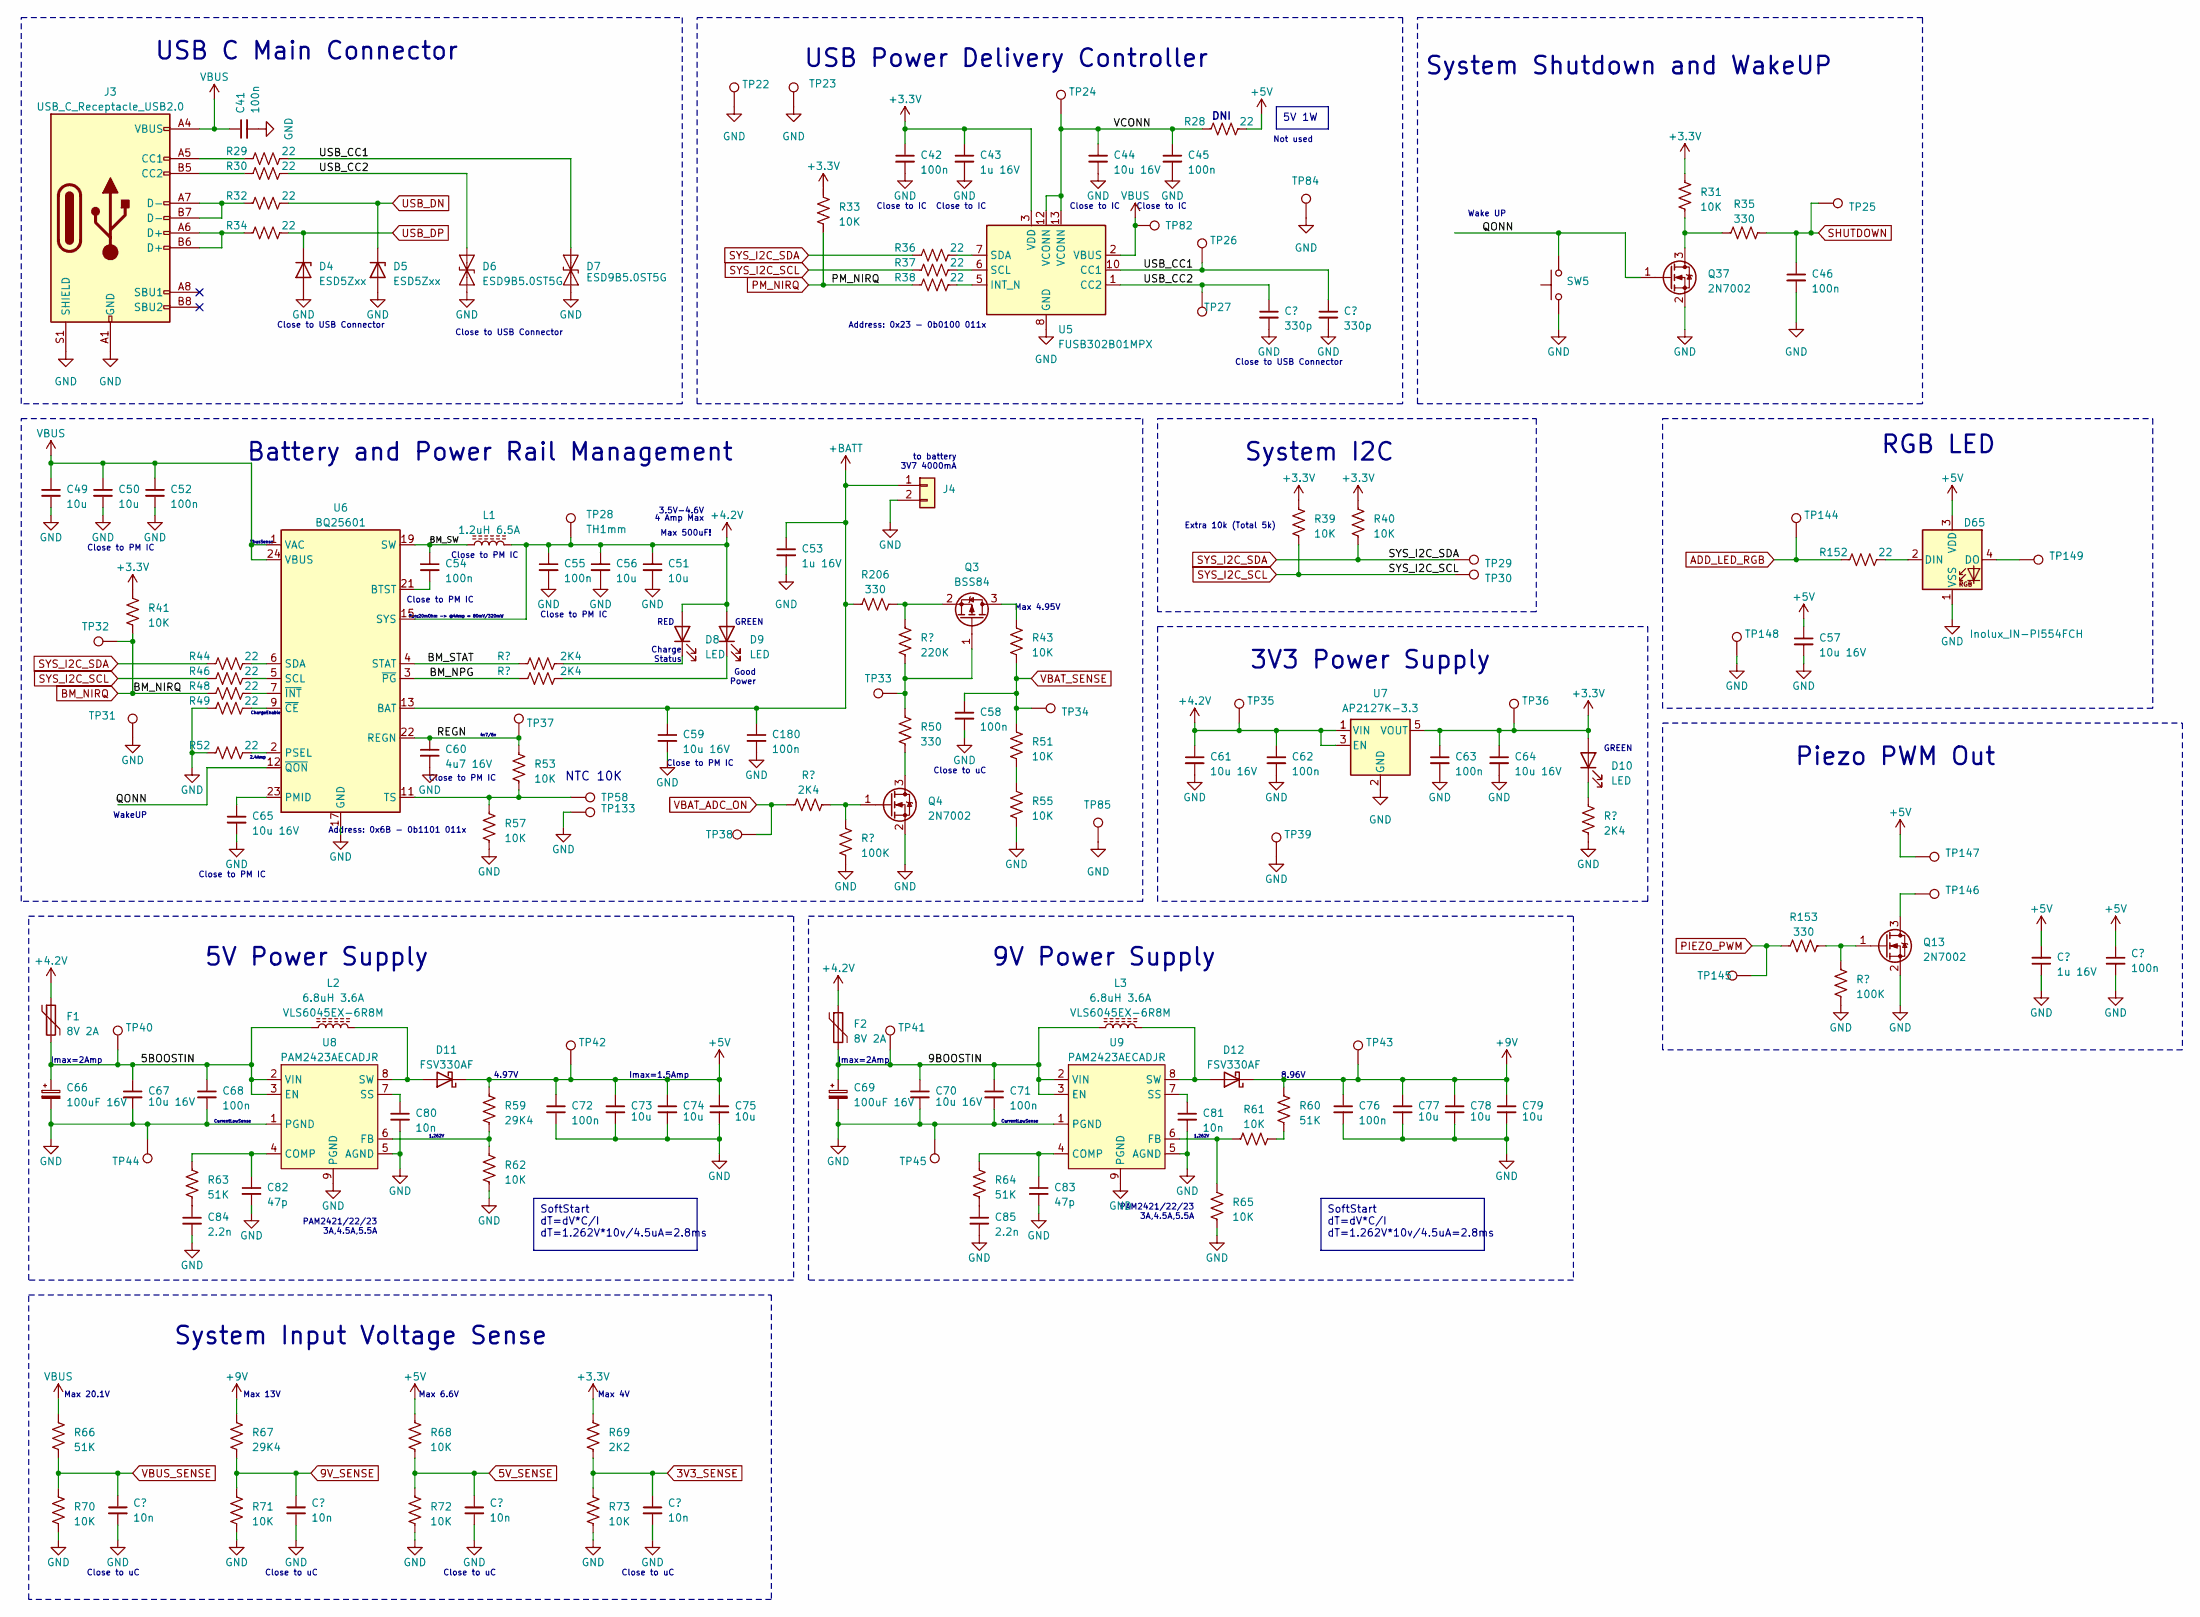
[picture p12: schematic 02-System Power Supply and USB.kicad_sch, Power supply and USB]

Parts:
C41, C42, C45, C46, C52, C54, C55, C58, C62, C63, C68, C71, C72, C76, C93, C180: 100n; C_0402_1005Metric
C43, C53, C92: 1u 16V; C_0603_1608Metric
C44, C57, C59, C61, C64, C65, C67, C70: 10u 16V; C_0805_2012Metric
C47, C48: 330p; C_0402_1005Metric
C49, C50, C51, C56, C73, C74, C75, C77, C78, C79: 10u; C_0805_2012Metric
C60: 4u7 16V; C_0603_1608Metric
C66, C69: 100uF 16V; CP_Elec_6.3x5.2
C80, C81, C86, C87, C88, C89: 10n; C_0402_1005Metric
C82, C83: 47p; C_0402_1005Metric
C84, C85: 2.2n; C_0402_1005Metric
D4, D5: ESD5Zxx; D_SOD-523
D6, D7: ESD9B5.0ST5G; D_SOD-923
D8, D9, D10: LED; LED_0402_1005Metric
D11, D12: FSV330AF; D_SOD-128
D65: Inolux_IN-PI554FCH; LED_Inolux_IN-PI554FCH_PLCC4_5.0x5.0mm_P3.2mm
F1, F2: 8V 2A; R_1812_4532Metric
J3: USB_C_Receptacle_USB2.0; USB_C_Receptacle_Palconn_UTC16-G
J4: Conn_01x02; JST_PH_B2B-PH-K_1x02_P2.00mm_Vertical
L1: 1.2uH 6.5A; L_Chilisin_BMRA00050520
L2, L3: 6.8uH 3.6A; L_Ferrocore_DLG-0504
Q3: BSS84; SOT-23
Q4, Q13, Q37: 2N7002; SOT-23
R28, R29, R30, R32, R34, R36, R37, R38, R44, R46, R48, R49, R52, R152: 22; R_0402_1005Metric
R31, R33, R39, R40, R41, R43, R51, R53, R55, R57, R61, R62, R65, R68, R70, R71, R72, R73: 10K; R_0402_1005Metric
R35, R50, R153, R206: 330; R_0402_1005Metric
R45, R47, R54, R56: 2K4; R_0402_1005Metric
R58, R154: 100K; R_0402_1005Metric
R59, R67: 29K4; R_0402_1005Metric
R60, R63, R64, R66: 51K; R_0402_1005Metric
R69: 2K2; R_0402_1005Metric
R168: 220K; R_0402_1005Metric
SW5: SW_Omron_B3FS; SW_Push_1P1T_NO_6x6mm_H9.5mm
TP22, TP24, TP25, TP26, TP27, TP29, TP30, TP31, TP32, TP33, TP34, TP35, TP36, TP37, TP38, TP39, TP40, TP41, TP42, TP43, TP44, TP45, TP58, TP82, TP84, TP85, TP144, TP145, TP148: S1mm; TestPoint_Pad_1.0x1.0mm
TP23, TP28, TP133, TP146, TP147, TP149: TH1mm; TestPoint_THTPad_1.0x1.0mm_Drill0.5mm
U5: FUSB302B01MPX; WQFN-14-1EP_2.5x2.5mm_P0.5mm_EP1.45x1.45mm
U6: BQ25601; Texas_S-PWQFN-N24_EP2.7x2.7mm_ThermalVias
U7: AP2127K-3.3; SOT-23-5
U8, U9: PAM2423AECADJR; SOIC-8-1EP_3.9x4.9mm_P1.27mm_EP2.29x3mm_ThermalVias

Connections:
3V3_SENSE: C89.1, R69.1, R73.2; also elsewhere on the board
5V_SENSE: C88.1, R68.1, R72.2; also elsewhere on the board
9V_SENSE: C87.1, R67.1, R71.2; also elsewhere on the board
+3.3V: C42.1, C43.1, C63.1, C64.1, D10.2 (A), R31.2, R33.2, R39.2, R40.2, R41.2, R69.2, TP36.1, U5.3 (VDD), U5.4 (VDD), U7.5 (VOUT); also elsewhere on the board
+4V: C51.1, C55.1, C56.1, C61.1, C62.1, D8.2 (A), D9.2 (A), F1.1, F2.1, L1.2, TP28.1, TP35.1, U6.15 (SYS), U6.16 (SYS), U7.1 (VIN), U7.3 (EN)
+9V: C76.1, C77.1, C78.1, C79.1, D12.1 (K), R60.2, R67.2, TP43.1; also elsewhere on the board
+BATT: C53.1, C59.1, C180.1, J4.1, R206.1, U6.13 (BAT), U6.14 (BAT)
/02-System Power Supply and USB/5BOOSTIN: C66.1, C67.1, C68.1, F1.2, L2.1, TP40.1, U8.2 (VIN), U8.3 (EN)
/02-System Power Supply and USB/9BOOSTIN: C69.1, C70.1, C71.1, F2.2, L3.1, TP41.1, U9.2 (VIN), U9.3 (EN)
/02-System Power Supply and USB/BM_NPG: R47.1, U6.3 (~PG)
/02-System Power Supply and USB/BM_STAT: R45.1, U6.4 (STAT)
/02-System Power Supply and USB/BM_SW: C54.1, L1.1, U6.19 (SW), U6.20 (SW)
/02-System Power Supply and USB/REGN: C60.1, R53.2, TP37.1, U6.22 (REGN)
/02-System Power Supply and USB/USB_CC1: C48.1, D7.2 (A2), R29.2, TP26.1, U5.10 (CC1), U5.11 (CC1)
/02-System Power Supply and USB/USB_CC2: C47.1, D6.2 (A2), R30.2, TP27.1, U5.1 (CC2), U5.14 (CC2)
/02-System Power Supply and USB/VCONN: C44.1, C45.1, R28.1, TP24.1, U5.12 (VCONN), U5.13 (VCONN)
ADD_LED_RGB: R152.1, TP144.1; also elsewhere on the board
BM_NIRQ: R41.1, R48.1, TP32.1; also elsewhere on the board
unnamed: C84.1, R63.1
unnamed: C85.1, R64.1
unnamed: D8.1 (K), R45.2
unnamed: D9.1 (K), R47.2
unnamed: D10.1 (K), R56.2
unnamed: D11.2 (A), L2.2, U8.8 (SW)
unnamed: D12.2 (A), L3.2, U9.8 (SW)
unnamed: D65.2 (DIN), R152.2
unnamed: D65.4 (DO), TP149.1
unnamed: J3.A5 (CC1), R29.1
unnamed: J3.B5 (CC2), R30.1
unnamed: J3.A6 (D+), J3.B6 (D+), R34.1
unnamed: J3.A7 (D-), J3.B7 (D-), R32.1
unnamed: Q3.3 (D), R43.2
unnamed: Q4.3 (D), R50.2
unnamed: Q4.1 (G), R54.2, R58.2
unnamed: Q13.3 (D), TP146.1
unnamed: Q13.1 (G), R153.1, R154.2
unnamed: Q37.3 (D), R31.1, R35.2
unnamed: R51.1, R55.2
unnamed: R60.1, R61.1
unnamed: R38.2, U5.5 (INT_N)
unnamed: R37.2, U5.6 (SCL)
unnamed: R36.2, U5.7 (SDA)
unnamed: C54.2, U6.21 (BTST)
unnamed: C65.1, U6.23 (PMID)
unnamed: R52.2, U6.2 (PSEL)
unnamed: R46.2, U6.5 (SCL)
unnamed: R44.2, U6.6 (SDA)
unnamed: R53.1, R57.2, TP58.1, U6.11 (TS)
unnamed: R49.2, U6.9 (~CE)
unnamed: R48.2, U6.7 (~INT)
unnamed: C82.1, R63.2, U8.4 (COMP)
unnamed: R59.1, R62.2, U8.6 (FB)
unnamed: C80.1, U8.7 (SS)
unnamed: C83.1, R64.2, U9.4 (COMP)
unnamed: R61.2, R65.2, U9.6 (FB)
unnamed: C81.1, U9.7 (SS)
PIEZO_PWM: R153.2, TP145.1; also elsewhere on the board
PM_NIRQ: R33.1, R38.1; also elsewhere on the board
SHUTDOWN: C46.1, R35.1, TP25.1; also elsewhere on the board
SYS_I2C_SCL: R37.1, R39.1, R46.1, TP30.1; also elsewhere on the board
SYS_I2C_SDA: R36.1, R40.1, R44.1, TP29.1; also elsewhere on the board
USB_DN: D5.1 (K), R32.2; also elsewhere on the board
USB_DP: D4.1 (K), R34.2; also elsewhere on the board
VBAT_ADC_ON: R54.1, TP38.1; also elsewhere on the board
VBAT_SENSE: C58.1, R43.1, R51.2, TP34.1; also elsewhere on the board
VBUS_SENSE: C86.1, R66.1, R70.2; also elsewhere on the board

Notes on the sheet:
5V 1W
SoftStart dT=dV*C/I dT=1.262V*10v/4.5uA=2.8ms
3.5V-4.6V
System I2C
Close to PM IC
Imax=2Amp
Charge Status
Imax=1.5Amp
RGB LED
4.97V
Ron:20mOhm -> @4Amp = 80mV/320mW
Close to uC
USB Power Delivery Controller
Close to USB Connector
PAM2421/22/23 3A,4.5A,5.5A
Max 20.1V
Close to IC
Max 6.6V
ChargeEnable
Not used
Max 4.95V
VbusSense
9V Power Supply
WakeUP
Address: 0x6B - 0b1101 011x
2.4Amp
to battery 3V7 4000mA
System Input Voltage Sense
1.262V
5V Power Supply
4 Amp Max
USB C Main Connector
Max 13V
4v7/6v
System Shutdown and WakeUP
DNI
Address: 0x23 - 0b0100 011x
CurrentLowSense
NTC 10K
Piezo PWM Out

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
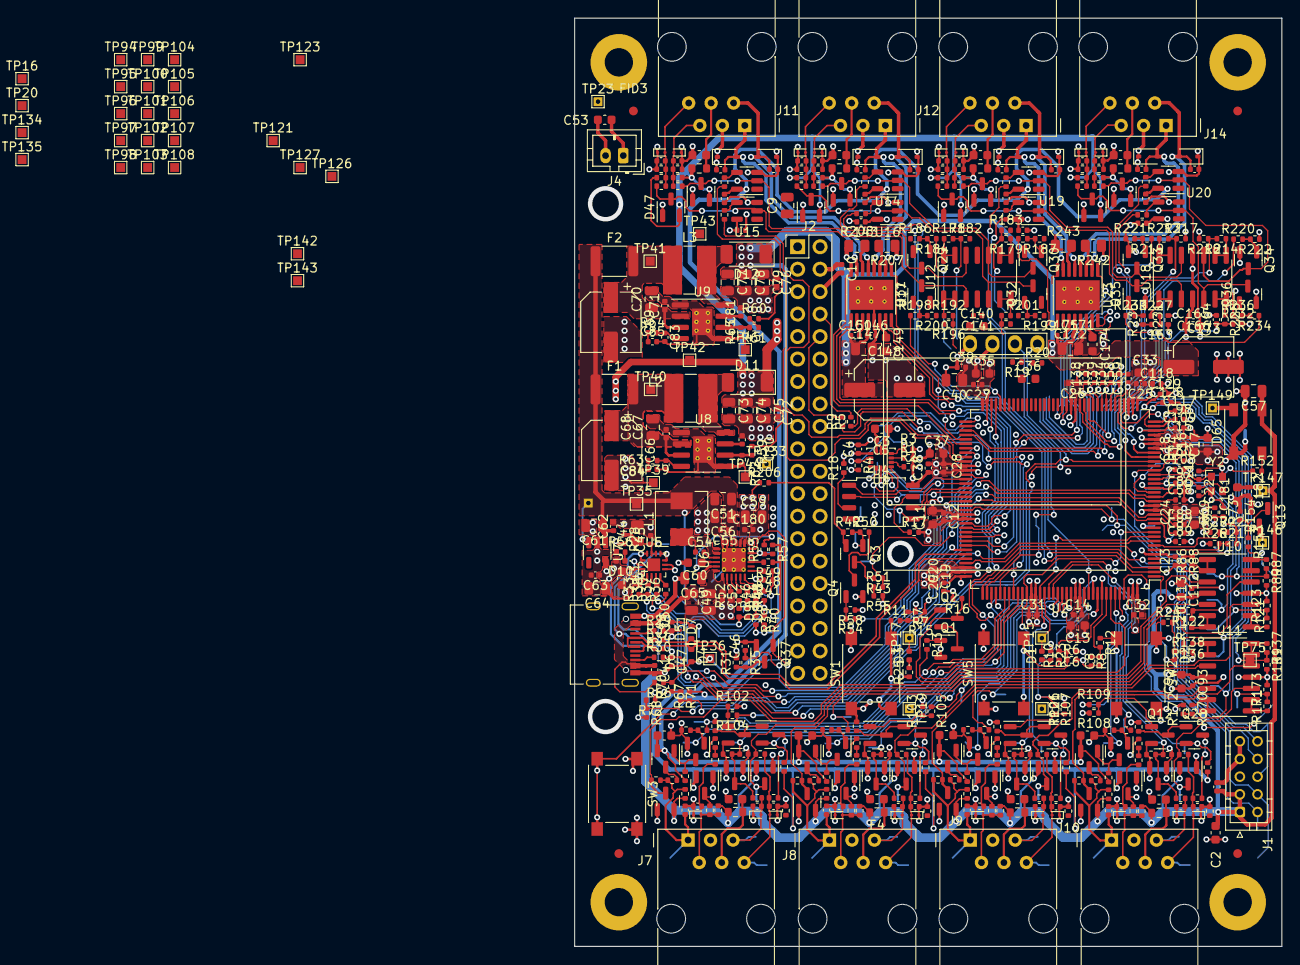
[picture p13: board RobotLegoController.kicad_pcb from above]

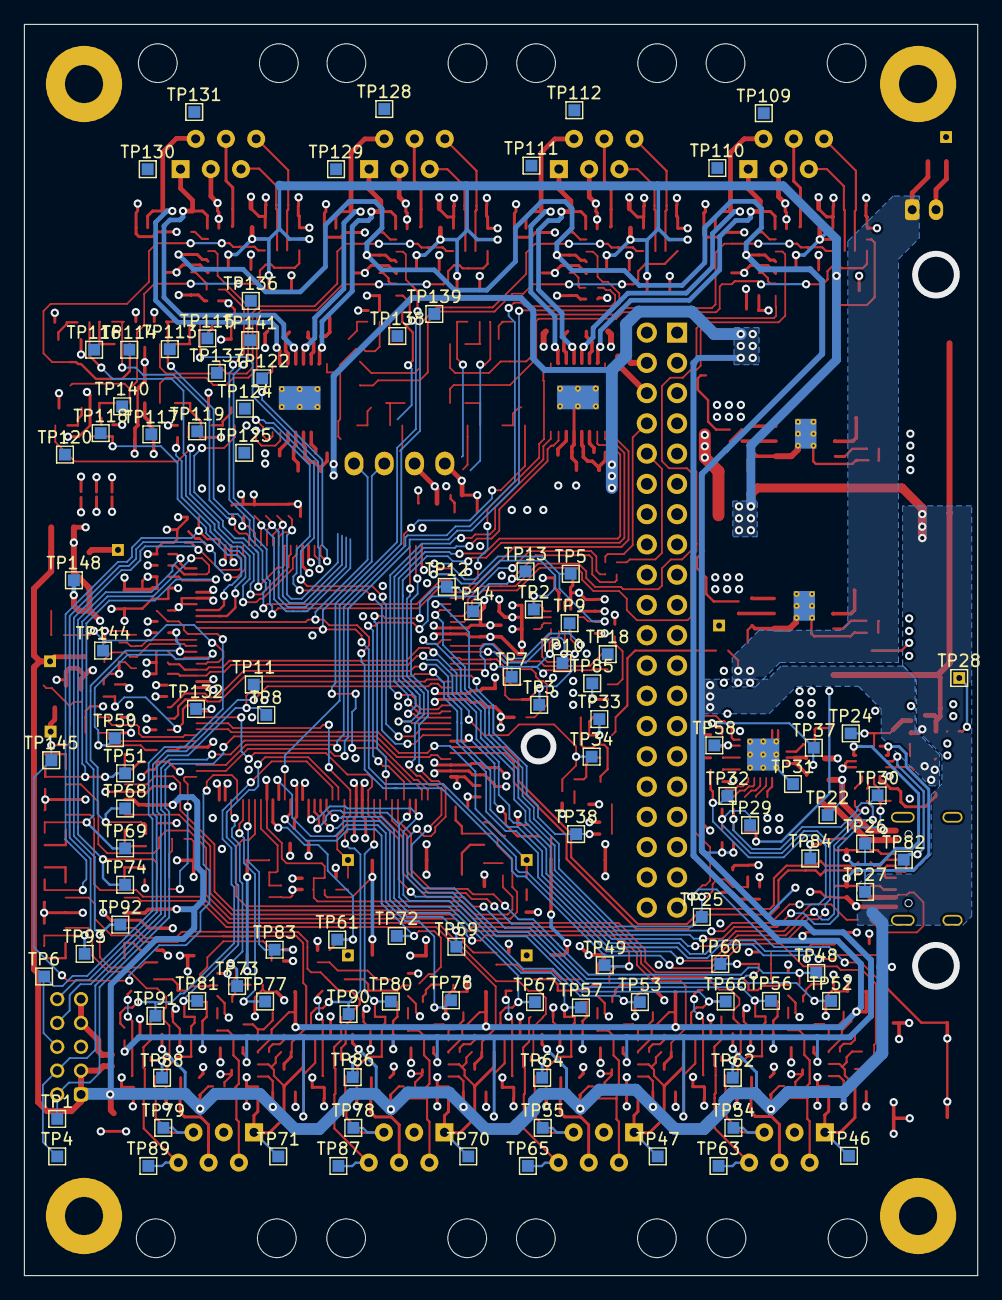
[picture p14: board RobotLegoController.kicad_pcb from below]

Board: 4 copper layers, 80.0 x 105.0 mm, 724 parts (105 on the bottom side), 301 nets.

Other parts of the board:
C9: 10u; C_0805_2012Metric
C133, C134, C138, C139, C158, C159, C163, C164: 10n; C_0402_1005Metric
C181: 1u 16V; C_0603_1608Metric
C182: 100n; C_0402_1005Metric
R42: 220K; R_0402_1005Metric
SW3: SW_Omron_B3FS; SW_Push_1P1T_NO_6x6mm_H9.5mm
TP136, TP137, TP138, TP139, TP140, TP141: S1mm; TestPoint_Pad_1.0x1.0mm

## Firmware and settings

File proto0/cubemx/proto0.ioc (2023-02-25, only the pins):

Mcu.UserName=STM32L4Q5CGTx
PA0.Signal=USART2_CTS
PA1.Signal=SDMMC2_CMD
PA10.Signal=USART1_RX
PA11.Signal=CAN1_RX
PA12.Signal=CAN1_TX
PA2.Signal=USART2_TX
PA3.Signal=USART2_RX
PA4.Signal=SPI1_NSS
PA5.Signal=SPI1_SCK
PA6.Signal=SPI1_MISO
PA7.Signal=I2C3_SCL
PA9.Signal=USART1_TX
PB10.Signal=SPI2_SCK
PB11.Signal=I2C2_SDA
PB12.Signal=SDMMC2_CK
PB13.Signal=I2C2_SCL
PB14.Signal=SDMMC2_D0
PB15.Signal=SPI2_MOSI
PB5.Signal=SPI1_MOSI
PB6.Signal=I2C4_SCL
PB7.Signal=I2C4_SDA
PB8.Signal=I2C1_SCL
PB9.Signal=I2C1_SDA

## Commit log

2022-10-23 mention ESP32 S3 too
2022-10-24 added a new smaller STM32 option
2022-11-02 add the cubeMX and the kicad file
    [ProtoZero.kicad_pcb, ProtoZero.kicad_sch]
2022-11-21 add power supply to MCU
    [ProtoZero.kicad_sch]
2022-11-21 add reset button and anti-bouncing capacitor
    [ProtoZero.kicad_sch]
2022-11-21 add boot switch
    [ProtoZero.kicad_sch]
2022-11-21 improve layout
    [ProtoZero.kicad_sch]
2022-12-05 added more sheets and started doing the ports
    [ProtoZero.kicad_sch, sensor_and_motor_ports.kicad_sch]
2023-02-25 Add initial kicad pcb file
    [01-Microcontroller and Extras.kicad_sch, 02-System Power Supply and USB.kicad_sch, 03-System Inputs A.kicad_sch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]
2023-02-25 Change motor and inputs to A~D names instead of number, fix dipswich
    [01-Microcontroller and Extras.kicad_sch, 02-System Power Supply and USB.kicad_sch, 03-System Inputs A.kicad_sch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]
2023-02-25 Extra pcb routing
    [02-System Power Supply and USB.kicad_sch, RobotLegoController.kicad_pcb]
2023-02-25 More routing done on the pcb
    [01-Microcontroller and Extras.kicad_sch, 02-System Power Supply and USB.kicad_sch, 03-System Inputs A.kicad_sch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]
2023-02-26 Finish routing inputs
    [01-Microcontroller and Extras.kicad_sch, 02-System Power Supply and USB.kicad_sch, 03-System Inputs A.kicad_sch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]
2023-02-27 New pcb update on motor frontend
    [01-Microcontroller and Extras.kicad_sch, 02-System Power Supply and USB.kicad_sch, 03-System Inputs A.kicad_sch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]
2023-02-28 More pcb routing done
    [01-Microcontroller and Extras.kicad_sch, 05-System Outputs A.kicad_sch, 06-System Outputs B.kicad_sch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]
2023-03-01 More advance on pcb
    [01-Microcontroller and Extras.kicad_sch, 03-System Inputs A.kicad_sch, 04-System Inputs B.kicad_sch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]
2023-03-03 More and more pcb routing. Most input frontend done
    [01-Microcontroller and Extras.kicad_sch, 03-System Inputs A.kicad_sch, 04-System Inputs B.kicad_sch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]
2023-03-04 More and more pcb routing
    [01-Microcontroller and Extras.kicad_sch, 05-System Outputs A.kicad_sch, 06-System Outputs B.kicad_sch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]
2023-03-04 yeap, more time routing the PCB
    [01-Microcontroller and Extras.kicad_sch, 02-System Power Supply and USB.kicad_sch, RobotLegoController.kicad_pcb]
2023-03-06 Working on motor routing, now motor c and d are done
    [01-Microcontroller and Extras.kicad_sch, 02-System Power Supply and USB.kicad_sch, 05-System Outputs A.kicad_sch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]
2023-03-06 Add some 3v3 routing into the pcb
2023-03-07 Finishing connecting most of the nets
    [01-Microcontroller and Extras.kicad_sch, 05-System Outputs A.kicad_sch, 06-System Outputs B.kicad_sch]
2023-03-07 Mosly done with silkscreen
2023-03-08 PCB is finally done
    [RobotLegoController.kicad_sch]
2023-03-09 Done with schematic and pcb
    [01-Microcontroller and Extras.kicad_sch, 02-System Power Supply and USB.kicad_sch, 03-System Inputs A.kicad_sch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]
2023-03-14 Update board name
    [01-Microcontroller and Extras.kicad_sch, 02-System Power Supply and USB.kicad_sch, 03-System Inputs A.kicad_sch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]
2023-03-16 Add bom and intial p and p files
    [BOM-ALL.xlsx, BOM-JLCPCB.xlsx, BOMRobotLegoController.csv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]
2023-03-20 Update pcb, bom and p and p files
    [PickAndPlace.csv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]
2023-03-20 Rework bom
    [BOM-JLCPCB.xlsx, RobotLegoController2.csv]
2023-03-20 Finish PAP and BOM
    [BOM-JLCPCB.xlsx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]
